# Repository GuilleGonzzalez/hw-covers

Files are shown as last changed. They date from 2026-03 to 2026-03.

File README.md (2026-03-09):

# Covers

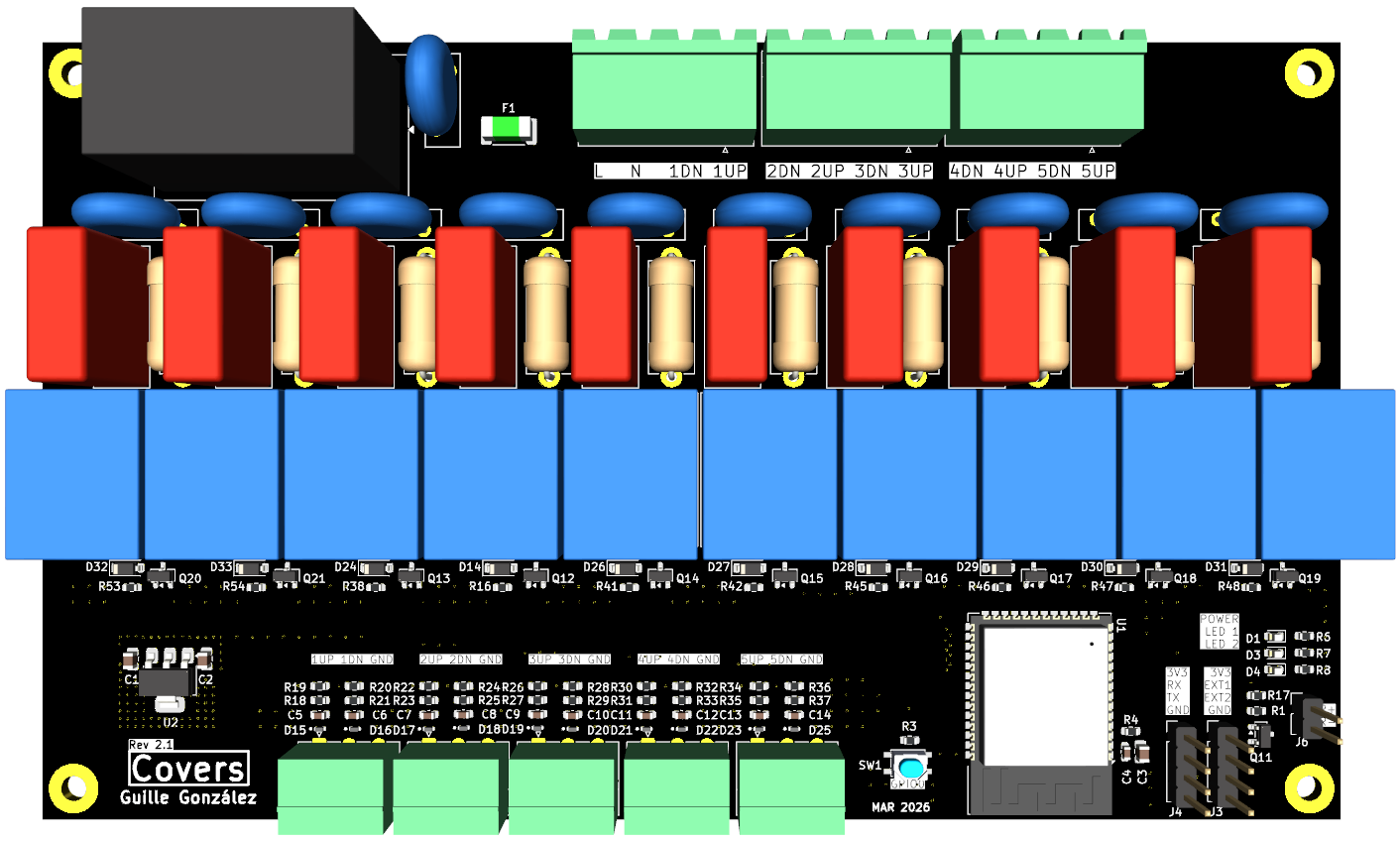
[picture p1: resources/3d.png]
PCB 3D


## Description

'Covers' is a PCB designed to control x5 covers with 10 relays and automatize it with [Home Assistant](https://www.home-assistant.io/).

Firmware used in this device is [tasmota](https://tasmota.github.io/docs/), an open source firmware for ESP devices.

## Power supply

The board is powered with a 230VAC power supply.

## Microprocessor

Espressif [ESP32-S3-WROOM](https://www.espressif.com/en/products/modules) module.

## LEDs

2 user LEDs. Functionality to define

## Relay Mode

**Circuit Safe**
* Relay1: ON/OFF
* Relay2: UP/DOWN

A RC snubber has been added for all relays to absorb voltage spikes

## Tasmota config

An example template will be uploaded when configured.

## Pin assignment

| PIN | Func |
| --- | --- |
| OUT1 | GPIO12  |
| DIR1 | GPIO11  |
| OUT2 | GPIO14  |
| DIR2 | GPIO13  |
| OUT3 | GPIO47  |
| DIR3 | GPIO21  |
| OUT4 | GPIO18  |
| DIR4 | GPIO08  |
| OUT5 | GPIO16  |
| DIR5 | GPIO17  |
| 1IN1 | GPIO09  |
| 1IN2 | GPIO10  |
| 2IN1 | GPIO19  |
| 2IN2 | GPIO20  |
| 3IN1 | GPIO40  |
| 3IN2 | GPIO39  |
| 4IN1 | GPIO42  |
| 4IN2 | GPIO41  |
| 5IN1 | GPIO01  |
| 5IN2 | GPIO02  |
| IR | GPIO06  |
| LED1 | GPIO15  |
| LED2 | GPIO07  |
| EXT1 | GPIO04  |
| EXT2 | GPIO05  |

## Enclosure

* Custom made.

## Changelog

All notable changes to this project will be documented in this section.

The format is based on [Keep a Changelog](https://keepachangelog.com/en/1.0.0/)

### [Unreleased]

### [2.1.0] - 2026-03-09

Fix some 2.0.0 rev issues

#### Added

* Add RC-snubbers values
* Add IR base resistor
* Add via stiching in regulator for power disipation

#### Fixed

* Fix L/N label text
* Isolate 230V AC lines from 5V DC lines

#### Changed

* Change relays transistor base from 1k to 470ohm

### [2.0.0] - 2026-03-08

Solved relay issue

#### Added

* Add RC snubbers
* Add schematic hierarchicals sheets

#### Fixed

* Change relays from 5A to 10A
* Change relay config to hardware-safe (output and direction) using form-C relays

#### Changed

* Change input resistor from 10k to 1k5
* Change ESP pin assignment

### [1.1.0] - 2025-02-28

Bug fixes

#### Added

* IR LED resistor value calculated: 180ohm

#### Fixed

* Relay NO/NC bug
* 1N4448W diode package fixed: SOD-123

#### Changed

* Better relays: 5A instead 3A, better pinout for clearance, thiner footprint
* HiLink symbol
* Rounded corners
* Components size: R/C 0603 instead 0402
* Inputs/outputs order: from left to right 1-5 in both cases

### [1.0.0] - 2025-02-05

First release

#### Added

* x5 covers

[Unreleased]: https://github.com/GuilleGonzzalez/hw-covers
[1.0.0]: https://github.com/GuilleGonzzalez/hw-covers/tree/v1.0.0
[1.1.0]: https://github.com/GuilleGonzzalez/hw-covers/tree/v1.1.0
[2.0.0]: https://github.com/GuilleGonzzalez/hw-covers/tree/v2.0.0
[2.1.0]: https://github.com/GuilleGonzzalez/hw-covers/tree/v2.1.0

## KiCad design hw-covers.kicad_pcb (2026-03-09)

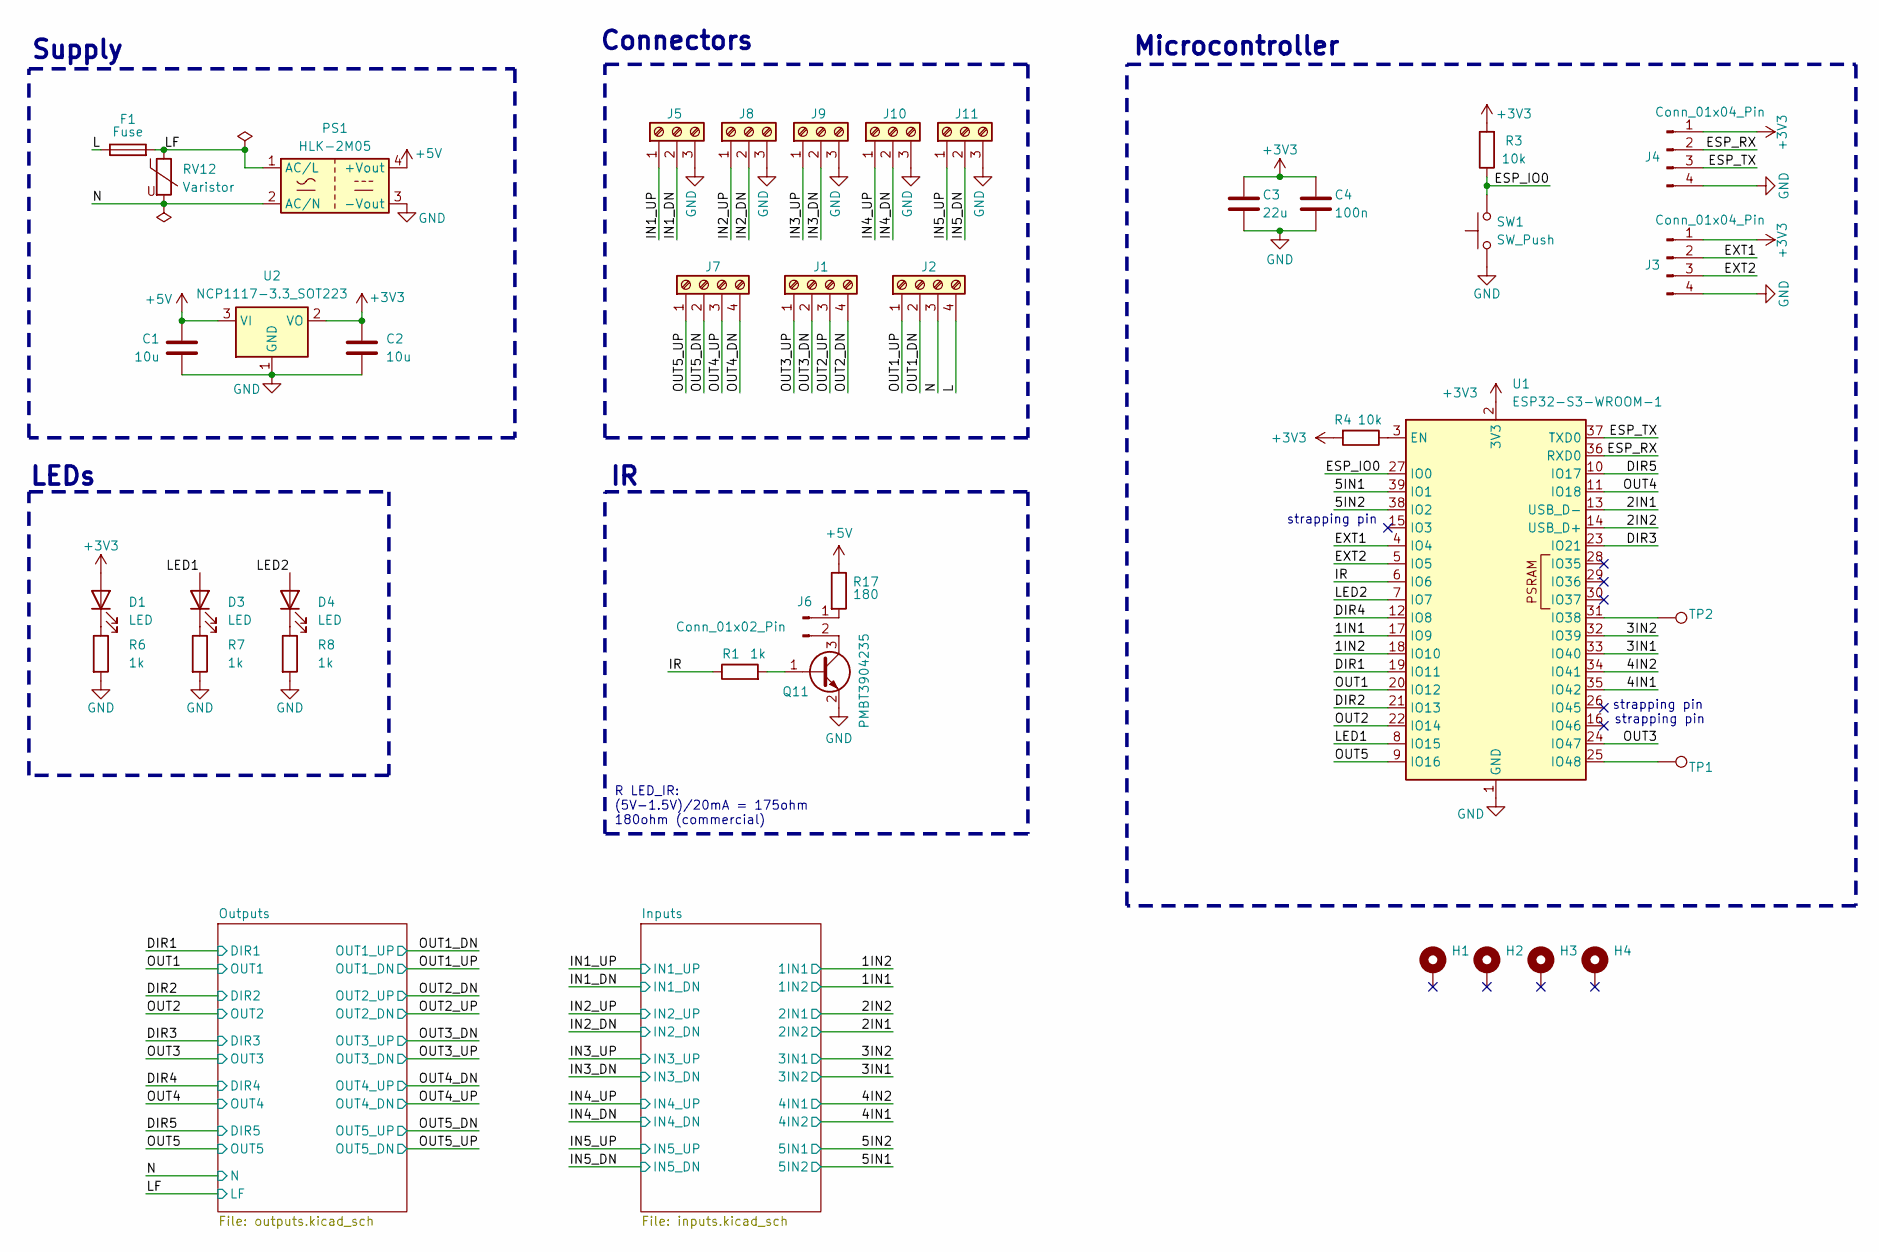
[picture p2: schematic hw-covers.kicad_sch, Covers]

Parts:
C1, C2: 10u; C_0805_2012Metric
C3: 22u; C_0805_2012Metric
C4: 100n; C_0603_1608Metric
D1, D3, D4: LED; LED_0603_1608Metric
F1: Fuse; Fuse_2512_6332Metric
H1, H2, H3, H4: MountingHole_3.2mm_M3_Pad
J1, J2, J7: Screw_Terminal_01x04; PhoenixContact_MSTBA_2,5_4-G-5,08_1x04_P5.08mm_Horizontal
J3, J4: Conn_01x04_Pin; PinHeader_1x04_P2.54mm_Vertical
J5, J8, J9, J10, J11: Screw_Terminal_01x03; PhoenixContact_MC_1,5_3-G-3.81_1x03_P3.81mm_Horizontal
J6: Conn_01x02_Pin; PinHeader_1x02_P2.54mm_Vertical
PS1: HLK-2M05; Converter_ACDC_Hi-Link_HLK-2Mxx
Q11: PMBT3904235; SOT-23; Manufacturer_PN PMBT3904,235
R1, R6, R7, R8: 1k; R_0603_1608Metric
R3, R4: 10k; R_0603_1608Metric
R17: 180; R_0603_1608Metric
RV12: Varistor; RV_Disc_D12mm_W4.5mm_P7.5mm
SW1: SW_Push; SW_SPST_PTS810
TP1, TP2: TestPoint; TestPoint_Pad_D1.5mm
U1: ESP32-S3-WROOM-1
U2: NCP1117-3.3_SOT223; SOT-223-3_TabPin2

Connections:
+3V3: C2.1, C3.1, C4.1, D1.2 (A), J3.1, J4.1, R3.2, R4.2, U1.2 (3V3), U2.2 (VO); also elsewhere on the board
+5V: C1.1, PS1.4 (+Vout), R17.1, U2.3 (VI); also elsewhere on the board
/1IN1: U1.17 (IO9); also elsewhere on the board
/1IN2: U1.18 (IO10); also elsewhere on the board
/2IN1: U1.13 (USB_D-); also elsewhere on the board
/2IN2: U1.14 (USB_D+); also elsewhere on the board
/3IN1: U1.33 (IO40); also elsewhere on the board
/3IN2: U1.32 (IO39); also elsewhere on the board
/4IN1: U1.35 (IO42); also elsewhere on the board
/4IN2: U1.34 (IO41); also elsewhere on the board
/5IN1: U1.39 (IO1); also elsewhere on the board
/5IN2: U1.38 (IO2); also elsewhere on the board
/DIR1: U1.19 (IO11); also elsewhere on the board
/DIR2: U1.21 (IO13); also elsewhere on the board
/DIR3: U1.23 (IO21); also elsewhere on the board
/DIR4: U1.12 (IO8); also elsewhere on the board
/DIR5: U1.10 (IO17); also elsewhere on the board
/ESP_IO0: R3.1, SW1.2, U1.27 (IO0)
/ESP_RX: J4.2, U1.36 (RXD0)
/ESP_TX: J4.3, U1.37 (TXD0)
/EXT1: J3.2, U1.4 (IO4)
/EXT2: J3.3, U1.5 (IO5)
/IN1_DN: J5.2; also elsewhere on the board
/IN1_UP: J5.1; also elsewhere on the board
/IN2_DN: J8.2; also elsewhere on the board
/IN2_UP: J8.1; also elsewhere on the board
/IN3_DN: J9.2; also elsewhere on the board
/IN3_UP: J9.1; also elsewhere on the board
/IN4_DN: J10.2; also elsewhere on the board
/IN4_UP: J10.1; also elsewhere on the board
/IN5_DN: J11.2; also elsewhere on the board
/IN5_UP: J11.1; also elsewhere on the board
/IR: R1.1, U1.6 (IO6)
/L: F1.1, J2.4
/LED1: D3.2 (A), U1.8 (IO15)
/LED2: D4.2 (A), U1.7 (IO7)
/LF: F1.2, PS1.1 (AC/L), RV12.1; also elsewhere on the board
/N: J2.3, PS1.2 (AC/N), RV12.2; also elsewhere on the board
/OUT1: U1.20 (IO12); also elsewhere on the board
/OUT1_DN: J2.2; also elsewhere on the board
/OUT1_UP: J2.1; also elsewhere on the board
/OUT2: U1.22 (IO14); also elsewhere on the board
/OUT2_DN: J1.4; also elsewhere on the board
/OUT2_UP: J1.3; also elsewhere on the board
/OUT3: U1.24 (IO47); also elsewhere on the board
/OUT3_DN: J1.2; also elsewhere on the board
/OUT3_UP: J1.1; also elsewhere on the board
/OUT4: U1.11 (IO18); also elsewhere on the board
/OUT4_DN: J7.4; also elsewhere on the board
/OUT4_UP: J7.3; also elsewhere on the board
/OUT5: U1.9 (IO16); also elsewhere on the board
/OUT5_DN: J7.2; also elsewhere on the board
/OUT5_UP: J7.1; also elsewhere on the board
GND: C1.2, C2.2, C3.2, C4.2, J3.4, J4.4, J5.3, J8.3, J9.3, J10.3, J11.3, PS1.3 (-Vout), Q11.2, R6.2, R7.2, R8.2, SW1.1, U1.1 (GND), U1.40 (GND), U1.41 (GND), U2.1 (GND); also elsewhere on the board
unnamed: D1.1 (K), R6.1
unnamed: D3.1 (K), R7.1
unnamed: D4.1 (K), R8.1
unnamed: J6.1, R17.2
unnamed: J6.2, Q11.3
unnamed: Q11.1, R1.2
unnamed: R4.1, U1.3 (EN)
unnamed: TP2.1, U1.31 (IO38)
unnamed: TP1.1, U1.25 (IO48)

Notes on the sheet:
Microcontroller
strapping pin
Supply
Connectors
R LED_IR: (5V-1.5V)/20mA = 175ohm 180ohm (commercial)
LEDs

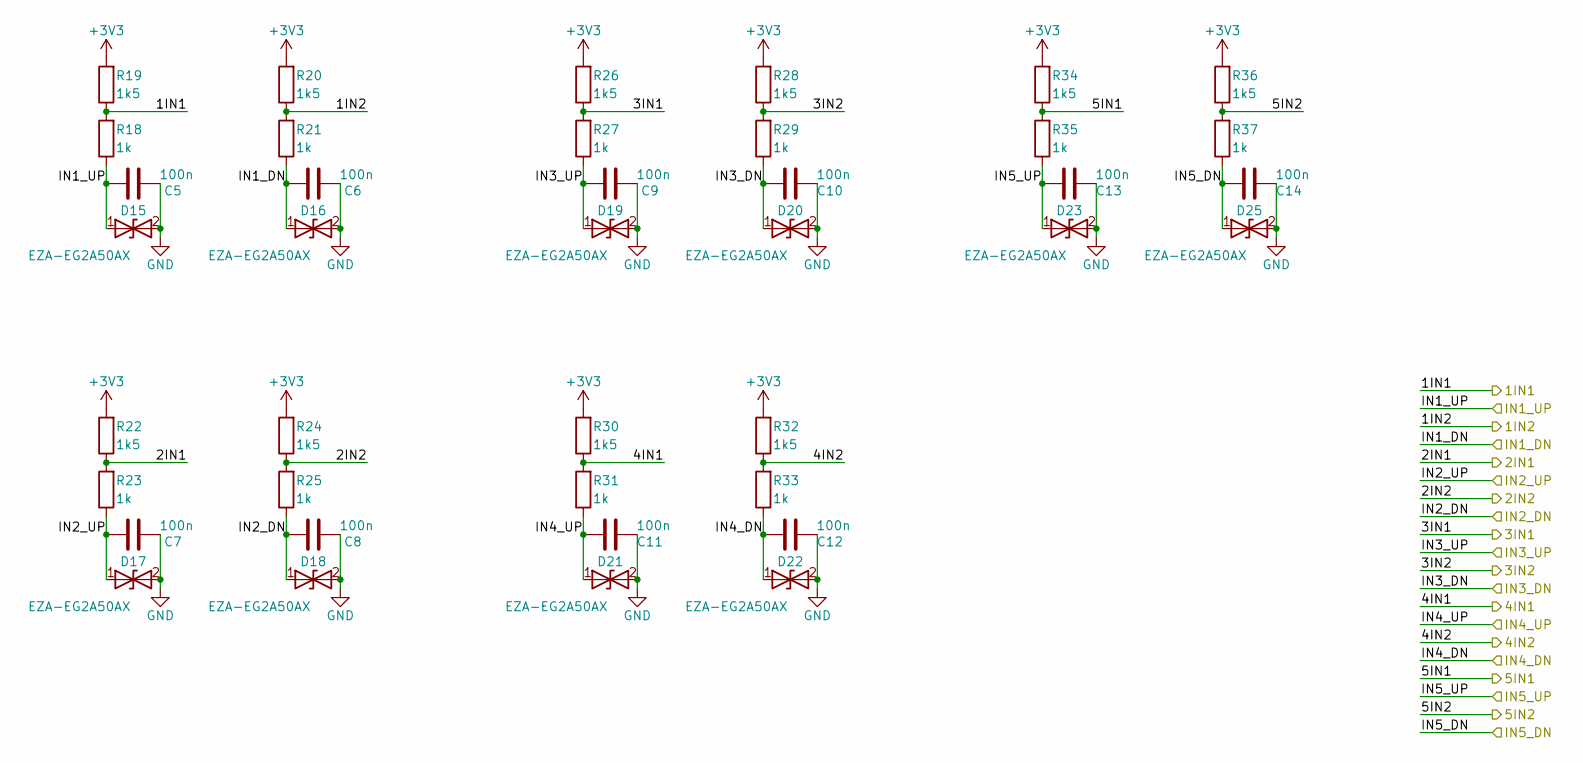
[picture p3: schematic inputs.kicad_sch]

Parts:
C5, C6, C7, C8, C9, C10, C11, C12, C13, C14: 100n; C_0603_1608Metric
D15, D16, D17, D18, D19, D20, D21, D22, D23, D25: EZA-EG2A50AX; EZAEG2A50AX; Manufacturer_Part_Number EZA-EG2A50AX; Mouser Part Number 667-EZA-EG2A50AX
R18, R21, R23, R25, R27, R29, R31, R33, R35, R37: 1k; R_0603_1608Metric
R19, R20, R22, R24, R26, R28, R30, R32, R34, R36: 1k5; R_0603_1608Metric

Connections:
+3V3: R19.2, R20.2, R22.2, R24.2, R26.2, R28.2, R30.2, R32.2, R34.2, R36.2; also elsewhere on the board
/1IN1: R20.1, R21.2; also elsewhere on the board
/1IN2: R18.2, R19.1; also elsewhere on the board
/2IN1: R24.1, R25.2; also elsewhere on the board
/2IN2: R22.1, R23.2; also elsewhere on the board
/3IN1: R28.1, R29.2; also elsewhere on the board
/3IN2: R26.1, R27.2; also elsewhere on the board
/4IN1: R32.1, R33.2; also elsewhere on the board
/4IN2: R30.1, R31.2; also elsewhere on the board
/5IN1: R36.1, R37.2; also elsewhere on the board
/5IN2: R34.1, R35.2; also elsewhere on the board
/IN1_DN: C6.1, D16.1 (A1), R21.1; also elsewhere on the board
/IN1_UP: C5.1, D15.1 (A1), R18.1; also elsewhere on the board
/IN2_DN: C8.1, D18.1 (A1), R25.1; also elsewhere on the board
/IN2_UP: C7.1, D17.1 (A1), R23.1; also elsewhere on the board
/IN3_DN: C10.1, D20.1 (A1), R29.1; also elsewhere on the board
/IN3_UP: C9.1, D19.1 (A1), R27.1; also elsewhere on the board
/IN4_DN: C12.1, D22.1 (A1), R33.1; also elsewhere on the board
/IN4_UP: C11.1, D21.1 (A1), R31.1; also elsewhere on the board
/IN5_DN: C14.1, D25.1 (A1), R37.1; also elsewhere on the board
/IN5_UP: C13.1, D23.1 (A1), R35.1; also elsewhere on the board
GND: C5.2, C6.2, C7.2, C8.2, C9.2, C10.2, C11.2, C12.2, C13.2, C14.2, D15.2 (A2), D16.2 (A2), D17.2 (A2), D18.2 (A2), D19.2 (A2), D20.2 (A2), D21.2 (A2), D22.2 (A2), D23.2 (A2), D25.2 (A2); also elsewhere on the board

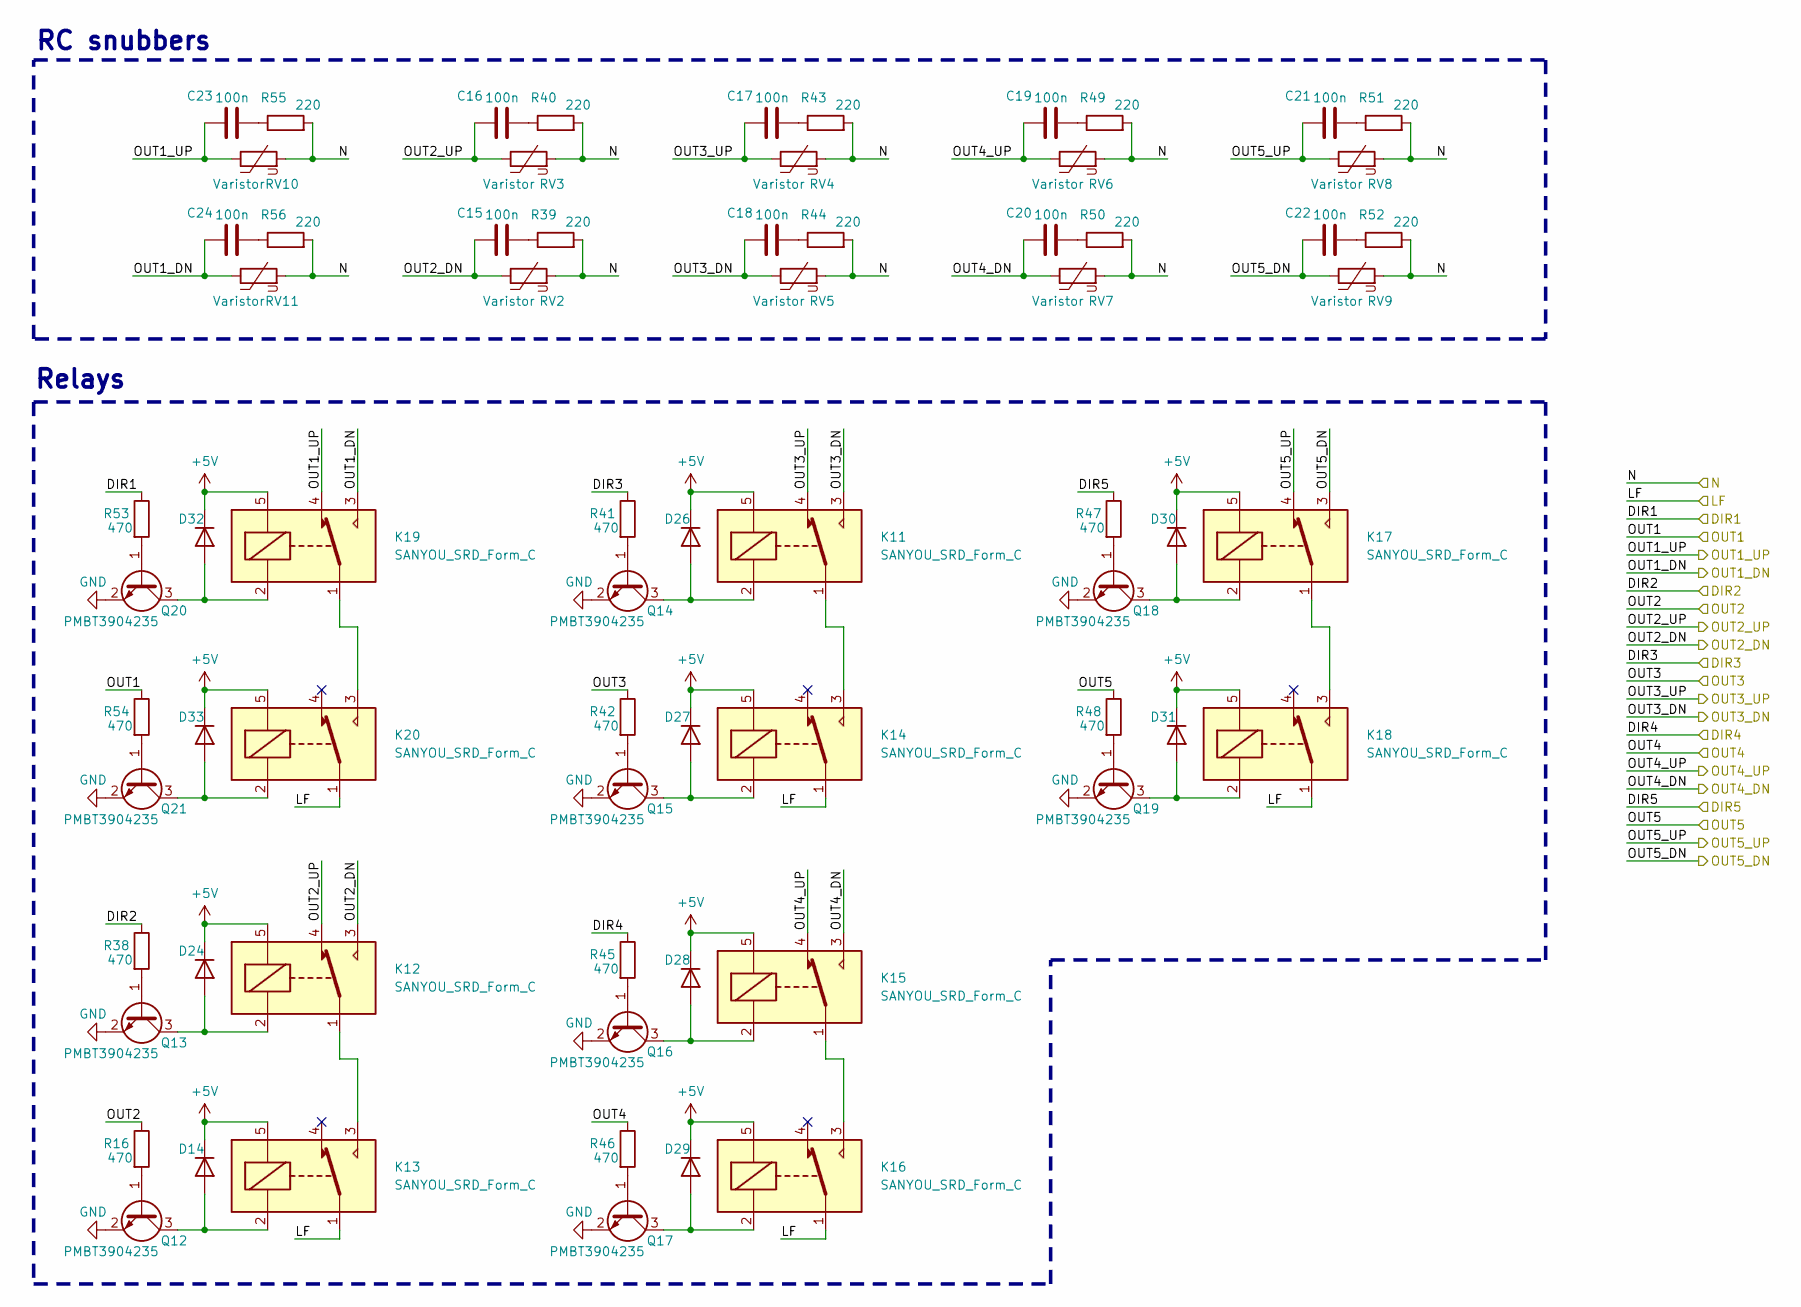
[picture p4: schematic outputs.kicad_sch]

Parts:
C15, C16, C17, C18, C19, C20, C21, C22, C23, C24: 100n; C_Rect_L18.0mm_W7.0mm_P15.00mm_FKS3_FKP3
D14, D24, D26, D27, D28, D29, D30, D31, D32, D33: 1N4448W; D_SOD-123
K11, K12, K13, K14, K15, K16, K17, K18, K19, K20: SANYOU_SRD_Form_C; Relay_SPDT_SANYOU_SRD_Series_Form_C
Q12, Q13, Q14, Q15, Q16, Q17, Q18, Q19, Q20, Q21: PMBT3904235; SOT-23; Manufacturer_PN PMBT3904,235
R16, R38, R41, R42, R45, R46, R47, R48, R53, R54: 470; R_0603_1608Metric
R39, R40, R43, R44, R49, R50, R51, R52, R55, R56: 220; R_Axial_DIN0614_L14.3mm_D5.7mm_P15.24mm_Horizontal
RV2, RV3, RV4, RV5, RV6, RV7, RV8, RV9, RV10, RV11: Varistor; RV_Disc_D12mm_W3.9mm_P7.5mm

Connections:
+5V: D14.1 (K), D24.1 (K), D26.1 (K), D27.1 (K), D28.1 (K), D29.1 (K), D30.1 (K), D31.1 (K), D32.1 (K), D33.1 (K), K11.5, K12.5, K13.5, K14.5, K15.5, K16.5, K17.5, K18.5, K19.5, K20.5; also elsewhere on the board
/DIR1: R53.1; also elsewhere on the board
/DIR2: R38.1; also elsewhere on the board
/DIR3: R41.1; also elsewhere on the board
/DIR4: R45.1; also elsewhere on the board
/DIR5: R47.1; also elsewhere on the board
/LF: K13.1, K14.1, K16.1, K18.1, K20.1; also elsewhere on the board
/N: R39.2, R40.2, R43.2, R44.2, R49.2, R50.2, R51.2, R52.2, R55.2, R56.2, RV2.2, RV3.2, RV4.2, RV5.2, RV6.2, RV7.2, RV8.2, RV9.2, RV10.2, RV11.2; also elsewhere on the board
/OUT1: R54.1; also elsewhere on the board
/OUT1_DN: C23.1, K19.4, RV10.1; also elsewhere on the board
/OUT1_UP: C24.1, K19.3, RV11.1; also elsewhere on the board
/OUT2: R16.1; also elsewhere on the board
/OUT2_DN: C16.1, K12.4, RV3.1; also elsewhere on the board
/OUT2_UP: C15.1, K12.3, RV2.1; also elsewhere on the board
/OUT3: R42.1; also elsewhere on the board
/OUT3_DN: C17.1, K11.4, RV4.1; also elsewhere on the board
/OUT3_UP: C18.1, K11.3, RV5.1; also elsewhere on the board
/OUT4: R46.1; also elsewhere on the board
/OUT4_DN: C19.1, K15.4, RV6.1; also elsewhere on the board
/OUT4_UP: C20.1, K15.3, RV7.1; also elsewhere on the board
/OUT5: R48.1; also elsewhere on the board
/OUT5_DN: C21.1, K17.4, RV8.1; also elsewhere on the board
/OUT5_UP: C22.1, K17.3, RV9.1; also elsewhere on the board
GND: Q12.2, Q13.2, Q14.2, Q15.2, Q16.2, Q17.2, Q18.2, Q19.2, Q20.2, Q21.2; also elsewhere on the board
unnamed: C15.2, R39.1
unnamed: C16.2, R40.1
unnamed: C17.2, R43.1
unnamed: C18.2, R44.1
unnamed: C19.2, R49.1
unnamed: C20.2, R50.1
unnamed: C21.2, R51.1
unnamed: C22.2, R52.1
unnamed: C23.2, R55.1
unnamed: C24.2, R56.1
unnamed: D14.2 (A), K13.2, Q12.3
unnamed: D24.2 (A), K12.2, Q13.3
unnamed: D26.2 (A), K11.2, Q14.3
unnamed: D27.2 (A), K14.2, Q15.3
unnamed: D28.2 (A), K15.2, Q16.3
unnamed: D29.2 (A), K16.2, Q17.3
unnamed: D30.2 (A), K17.2, Q18.3
unnamed: D31.2 (A), K18.2, Q19.3
unnamed: D32.2 (A), K19.2, Q20.3
unnamed: D33.2 (A), K20.2, Q21.3
unnamed: K11.1, K14.3
unnamed: K12.1, K13.3
unnamed: K15.1, K16.3
unnamed: K17.1, K18.3
unnamed: K19.1, K20.3
unnamed: Q12.1, R16.2
unnamed: Q13.1, R38.2
unnamed: Q14.1, R41.2
unnamed: Q15.1, R42.2
unnamed: Q16.1, R45.2
unnamed: Q17.1, R46.2
unnamed: Q18.1, R47.2
unnamed: Q19.1, R48.2
unnamed: Q20.1, R53.2
unnamed: Q21.1, R54.2

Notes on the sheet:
Relays
RC snubbers

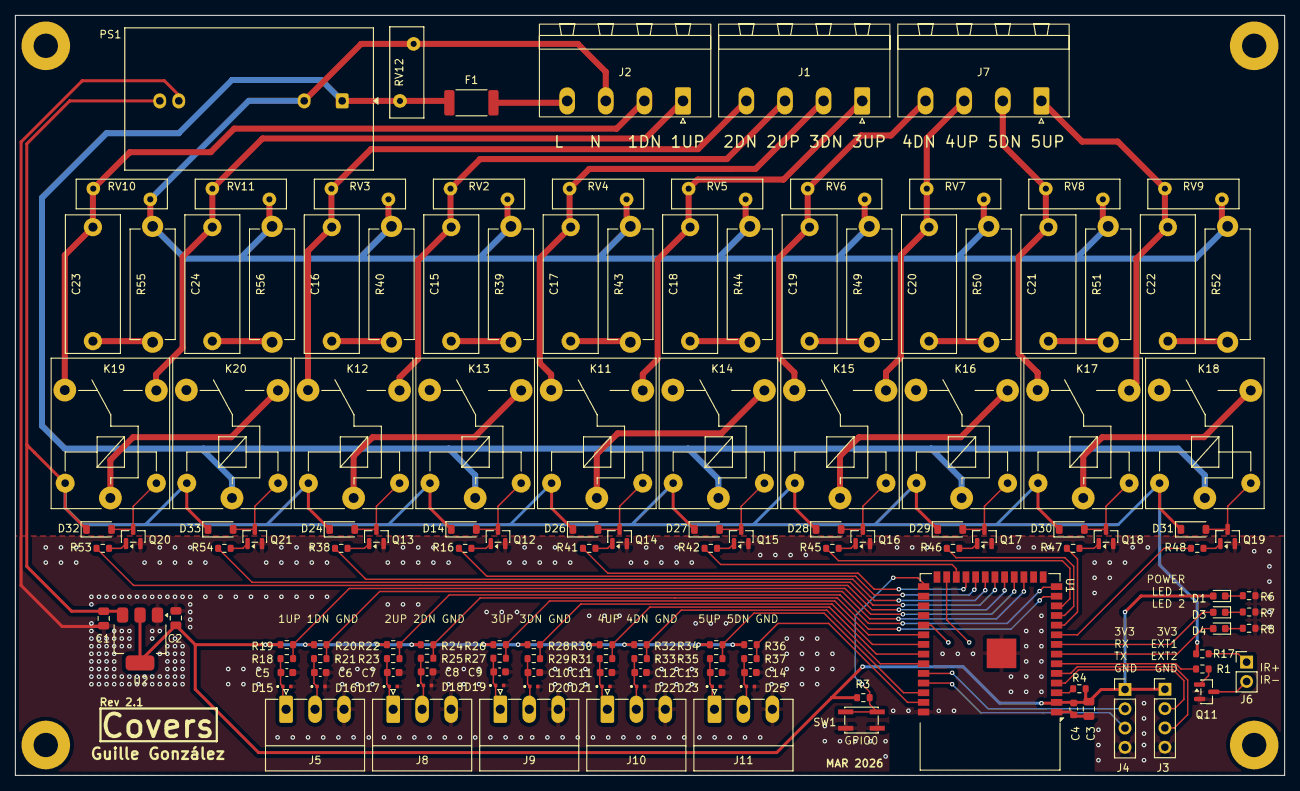
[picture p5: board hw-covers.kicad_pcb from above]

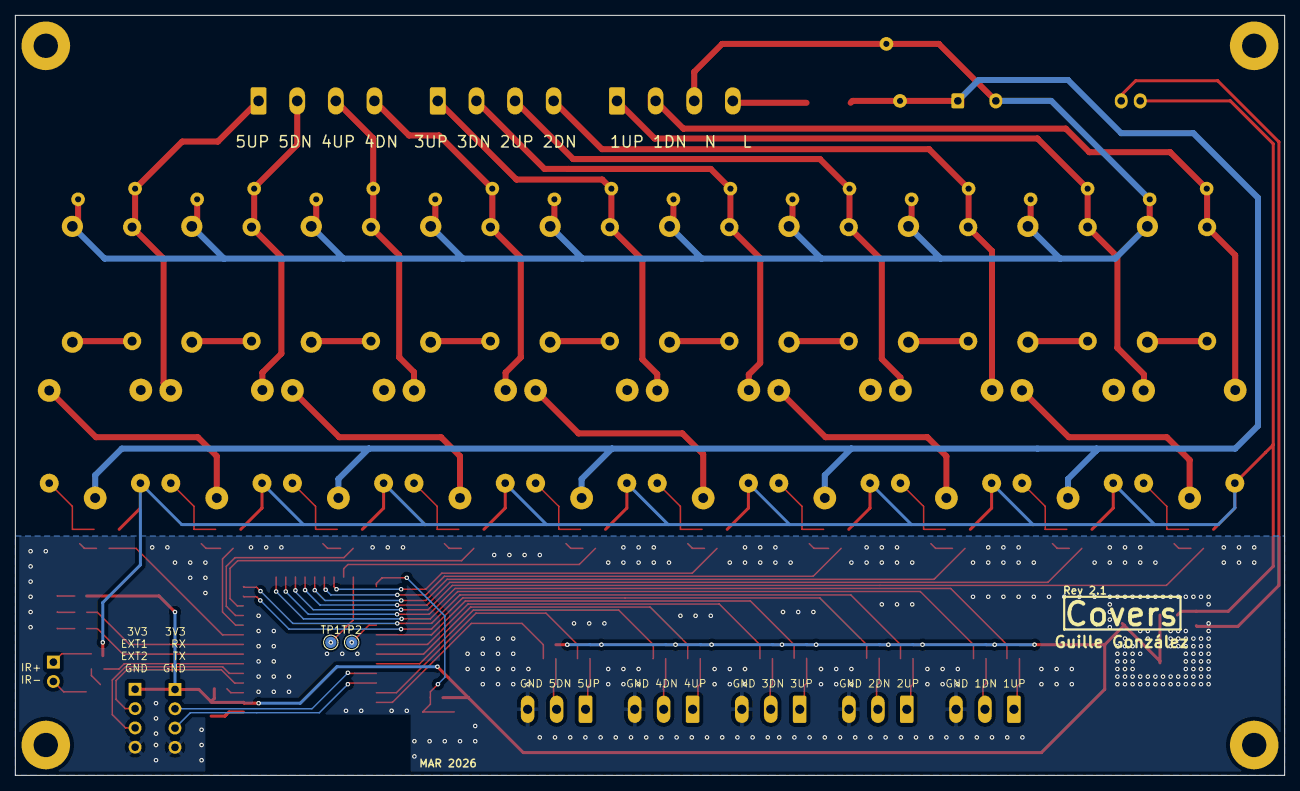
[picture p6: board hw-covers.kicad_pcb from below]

Board: 2 copper layers, 167.0 x 100.0 mm, 148 parts (2 on the bottom side), 98 nets.

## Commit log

2025-02-04 Finish sch and start with placement
    [hw-covers.kicad_pcb, hw-covers.kicad_sch]
2025-02-05 Release 1.0
    [hw-covers.kicad_pcb, hw-covers.kicad_sch]
2025-02-05 Change gerbers configuration
    [hw-covers.kicad_pcb]
2025-02-28 Release 1.1
    [hw-covers.kicad_pcb, hw-covers.kicad_sch]
2025-02-28 Minor changes to release 1.1
    [hw-covers.kicad_pcb]
2026-03-04 Sch update for rev 2
    [hw-covers.kicad_pcb, hw-covers.kicad_sch, inputs.kicad_sch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]
2026-03-05 Add placement
    [hw-covers.kicad_pcb, inputs.kicad_sch, outputs.kicad_sch]
2026-03-06 Change in R values and routing test
    [hw-covers.kicad_pcb, hw-covers.kicad_sch, outputs.kicad_sch]
2026-03-08 Finish routing
    [hw-covers.kicad_pcb, hw-covers.kicad_sch]
2026-03-08 Finish PCB
    [hw-covers.kicad_pcb, hw-covers.kicad_sch]
2026-03-08 Ready to release
    [hw-covers.kicad_pcb, hw-covers.kicad_sch]
2026-03-09 Release 2.1.0
    [hw-covers.kicad_pcb, hw-covers.kicad_sch, outputs.kicad_sch]
